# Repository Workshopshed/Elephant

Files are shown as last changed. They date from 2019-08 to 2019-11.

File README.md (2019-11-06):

# Elephant

This ESP32 controlled elephant was created for Diyode Magazine and was published in issue #26 and #28.  Daniel Koch took up the challenge to try to build this from my instructions and in the process we came up with a bunch of enhancements to make it easier to print and assemble. Daniel and Murray Roberts also ensured the wording of the instructions was top notch.

https://diyodemag.com/projects/part_1_walking_wildlife

https://diyodemag.com/projects/part_2_walking_wildlife

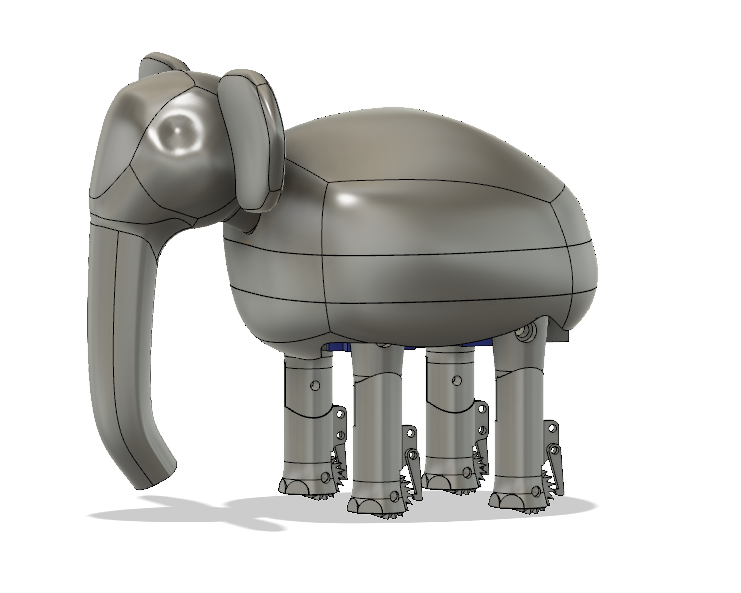
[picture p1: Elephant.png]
Elephant Model


The elephant is controlled from a simple web page hosted on the ESP32 and Ajax calls are used to respond to the buttons.

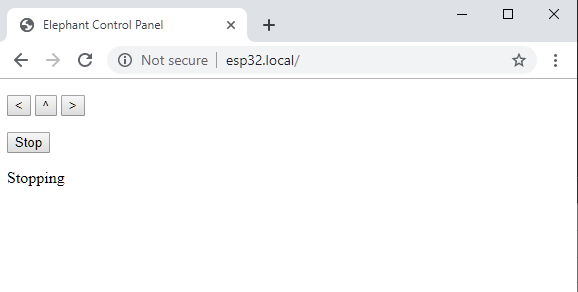
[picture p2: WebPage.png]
Web Page


A spin off project for the servo power distribution board also appeared in issue #26 with Daniel Koch providing a cloned version using stripboard.
https://diyodemag.com/projects/servo_power

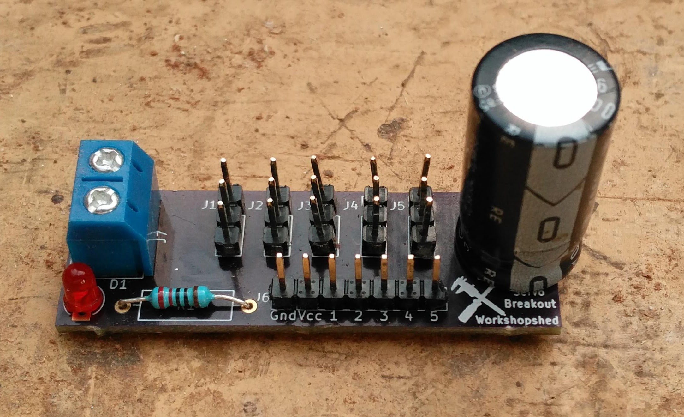
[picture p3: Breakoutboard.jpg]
Breakout Board


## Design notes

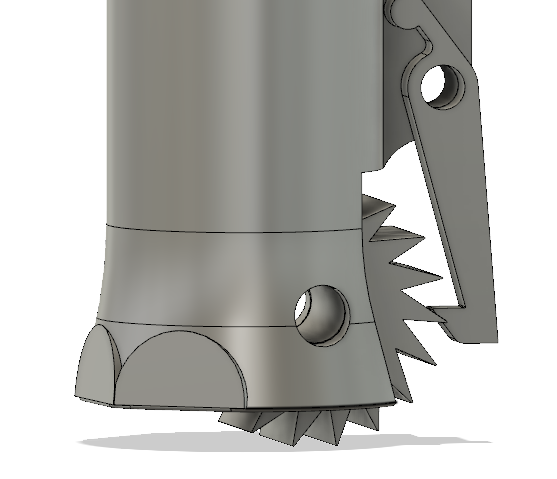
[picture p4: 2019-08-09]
RatchettMechanism.png

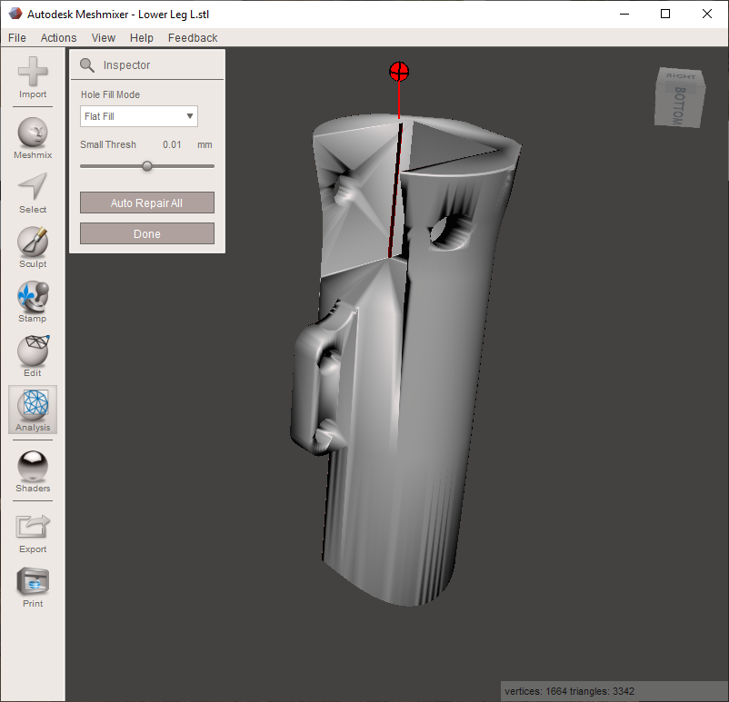
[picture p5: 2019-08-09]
MeshMixer.png

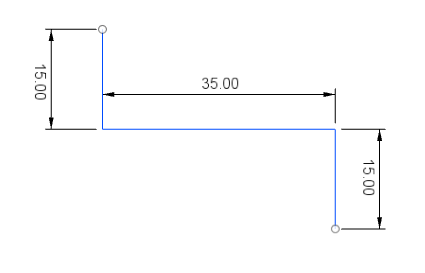
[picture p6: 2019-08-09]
WireTemplate.png

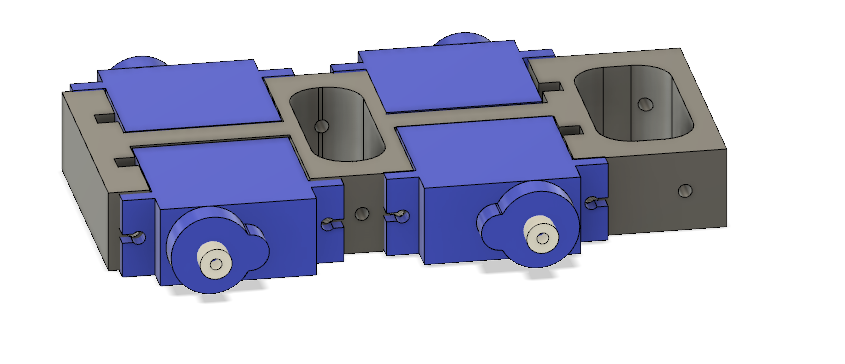
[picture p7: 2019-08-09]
Servos.png

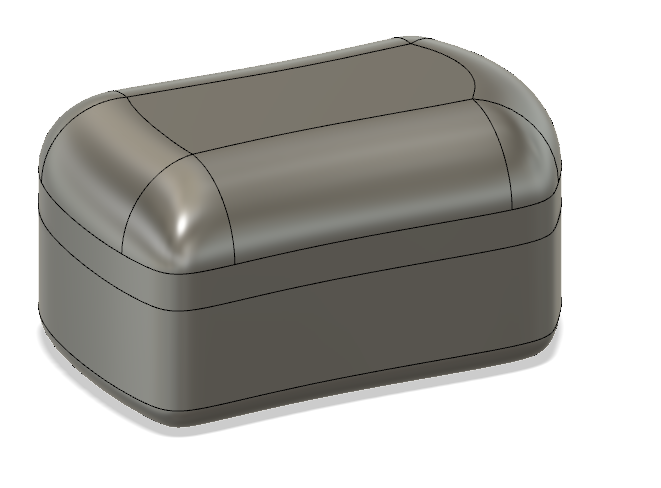
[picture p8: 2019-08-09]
SparePics/Boxy.png

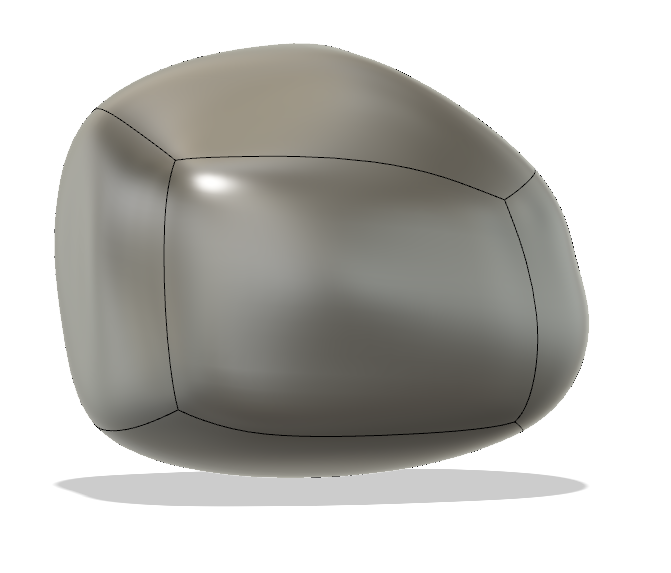
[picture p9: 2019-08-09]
SparePics/Form.png

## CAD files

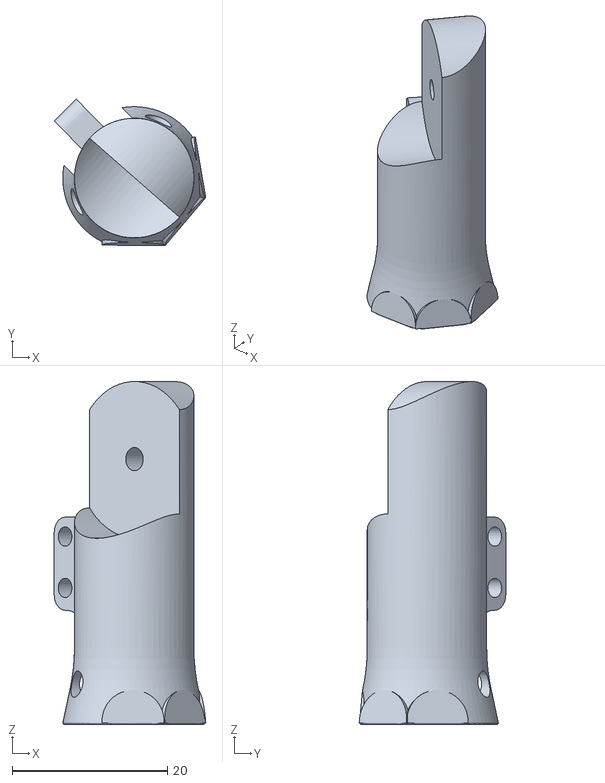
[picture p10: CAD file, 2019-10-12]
Models/Lower Leg L.stl
19.5 x 18.9 x 44.2

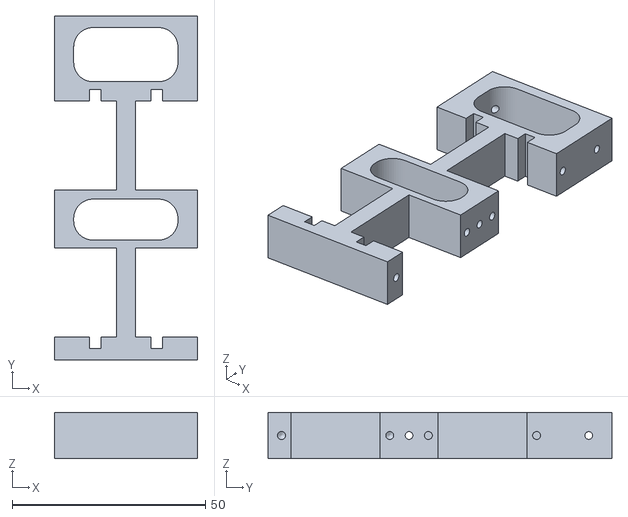
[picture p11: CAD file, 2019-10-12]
Models/Chassis.stl
37.0 x 89.0 x 12.0

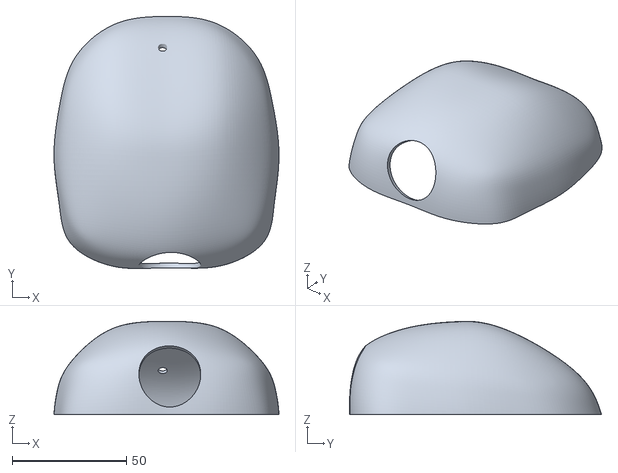
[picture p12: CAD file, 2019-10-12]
Models/Upper Body.stl
98.3 x 110.1 x 40.8

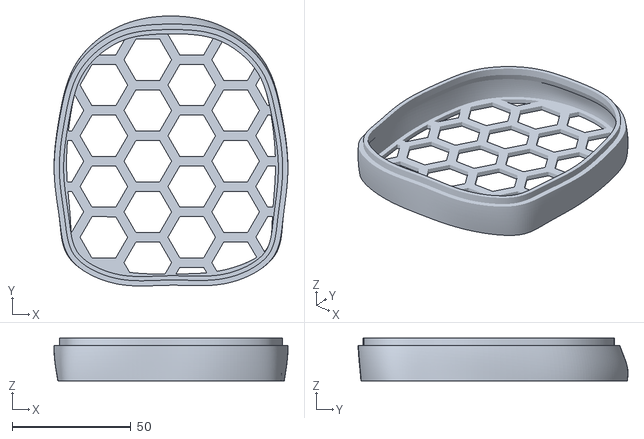
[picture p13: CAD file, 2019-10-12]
Models/Middle Body.stl
98.3 x 113.5 x 17.9

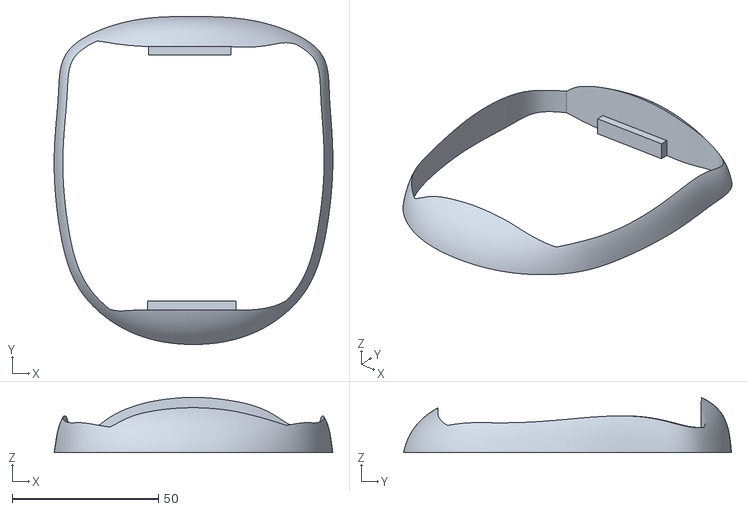
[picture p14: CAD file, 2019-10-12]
Models/Lower Body.stl
95.2 x 112.0 x 18.8

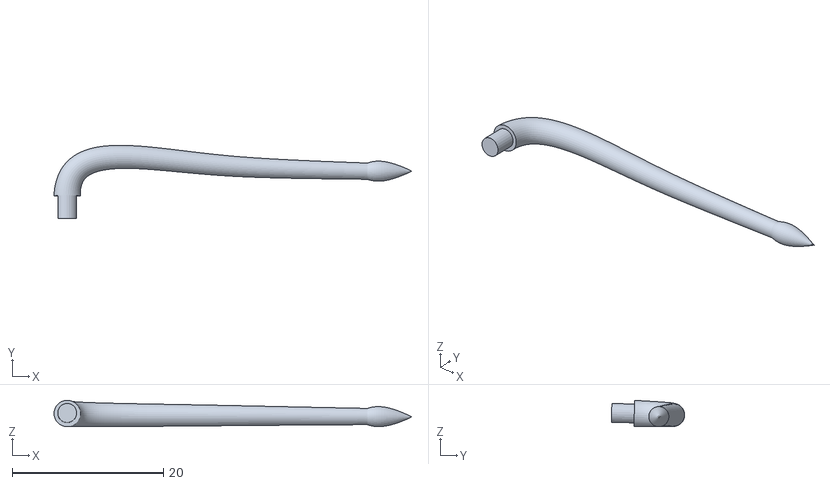
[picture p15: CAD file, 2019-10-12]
Models/Tail.stl
47.4 x 9.71 x 3.49

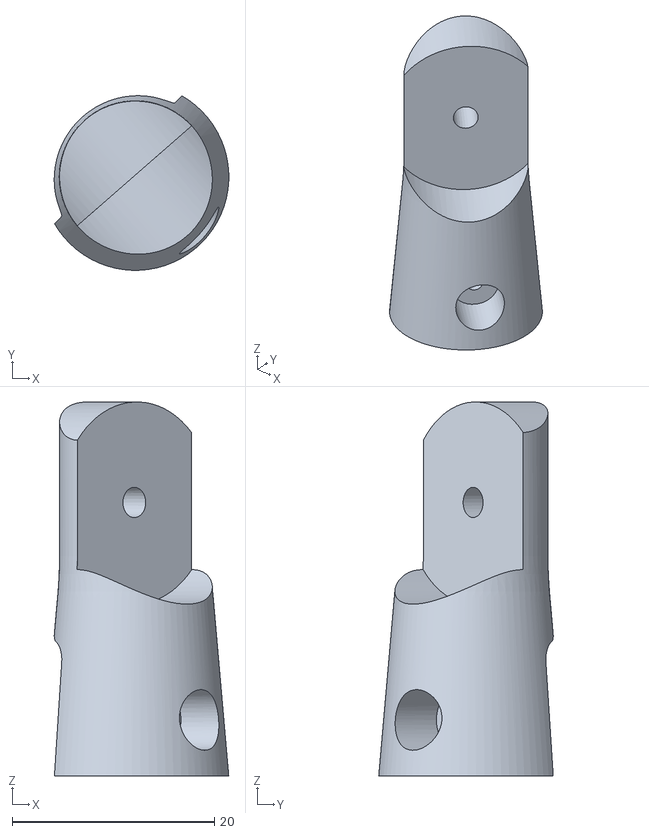
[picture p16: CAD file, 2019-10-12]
Models/Upper Leg.stl
17.3 x 17.3 x 37.0

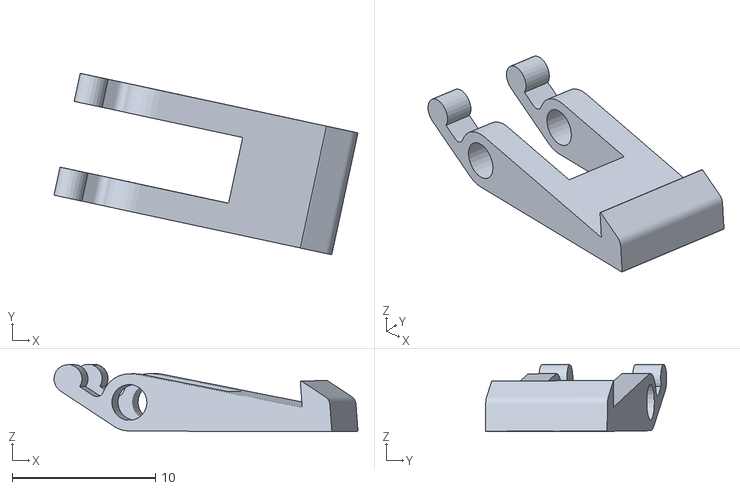
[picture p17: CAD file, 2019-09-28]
Models/Pawl.stl
21.2 x 12.7 x 4.71

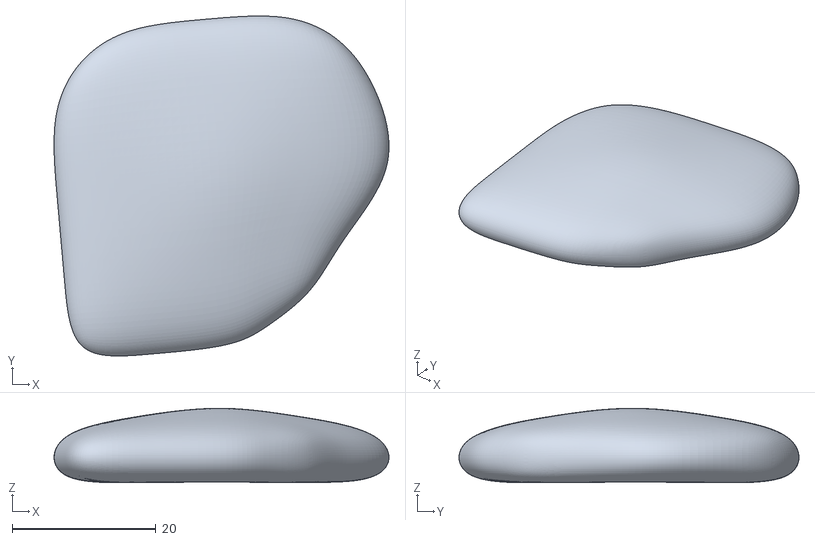
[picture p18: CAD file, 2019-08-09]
Models/EarR.stl
46.7 x 47.4 x 10.4

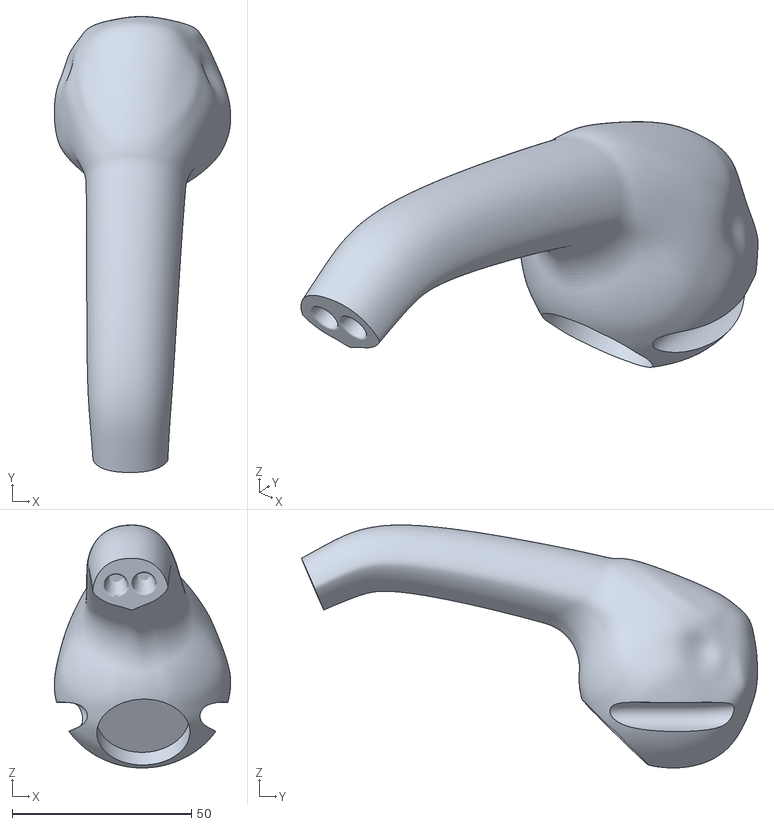
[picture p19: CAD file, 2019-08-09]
Models/Head.stl
49.2 x 127.2 x 67.8

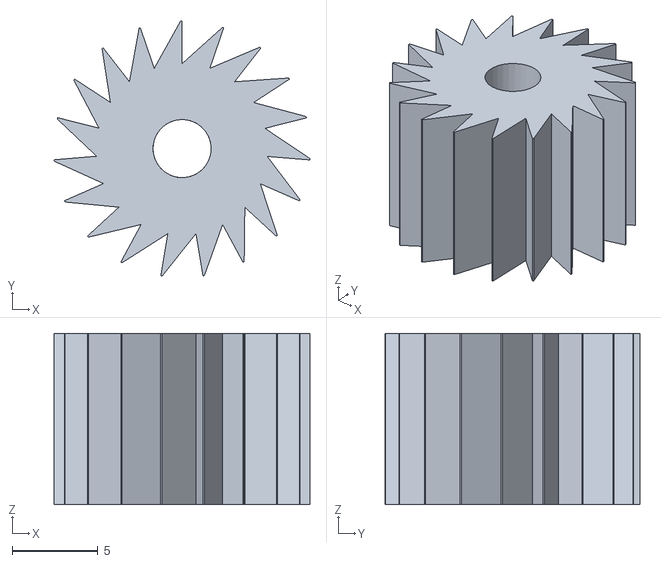
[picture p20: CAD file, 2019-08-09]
Models/Wheel.stl
15.0 x 14.9 x 10.0

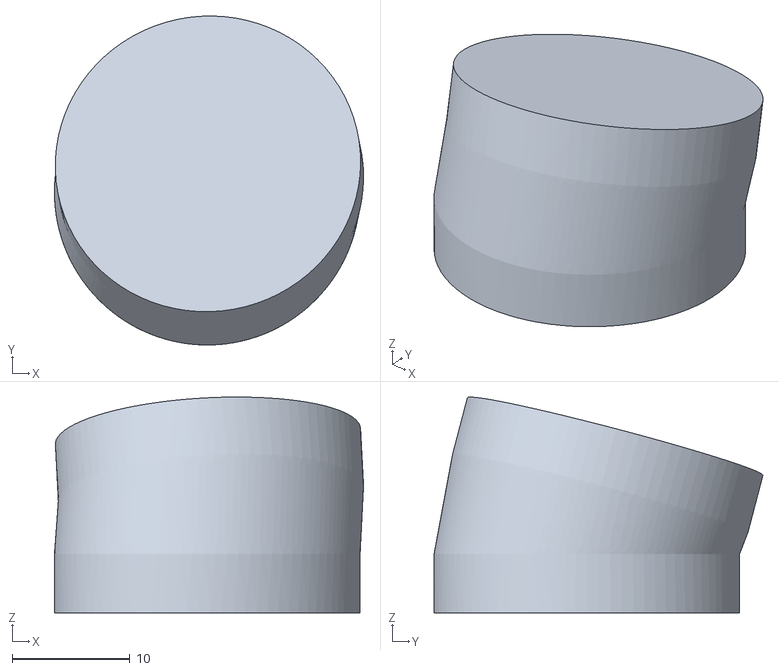
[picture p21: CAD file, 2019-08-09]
Models/Neck.stl
26.3 x 28.0 x 18.4

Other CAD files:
Models/Lower Leg R.stl
Models/EarL.stl

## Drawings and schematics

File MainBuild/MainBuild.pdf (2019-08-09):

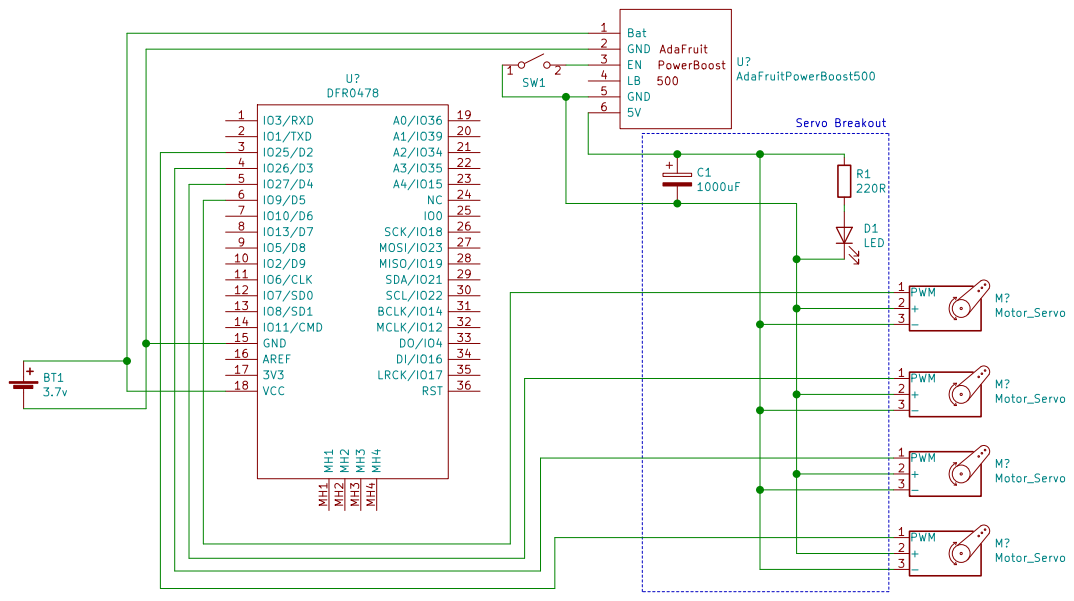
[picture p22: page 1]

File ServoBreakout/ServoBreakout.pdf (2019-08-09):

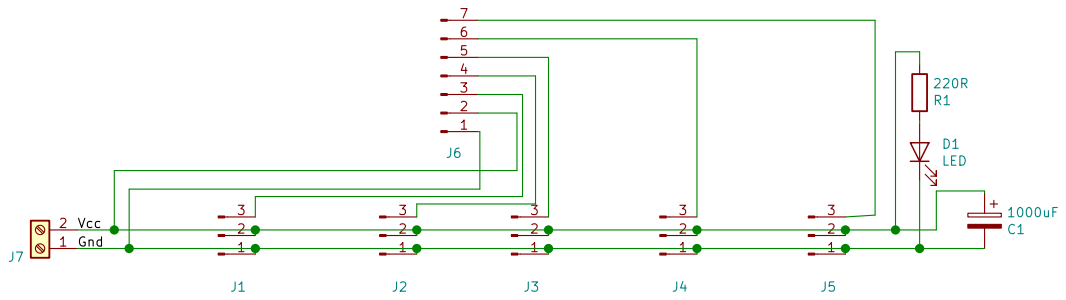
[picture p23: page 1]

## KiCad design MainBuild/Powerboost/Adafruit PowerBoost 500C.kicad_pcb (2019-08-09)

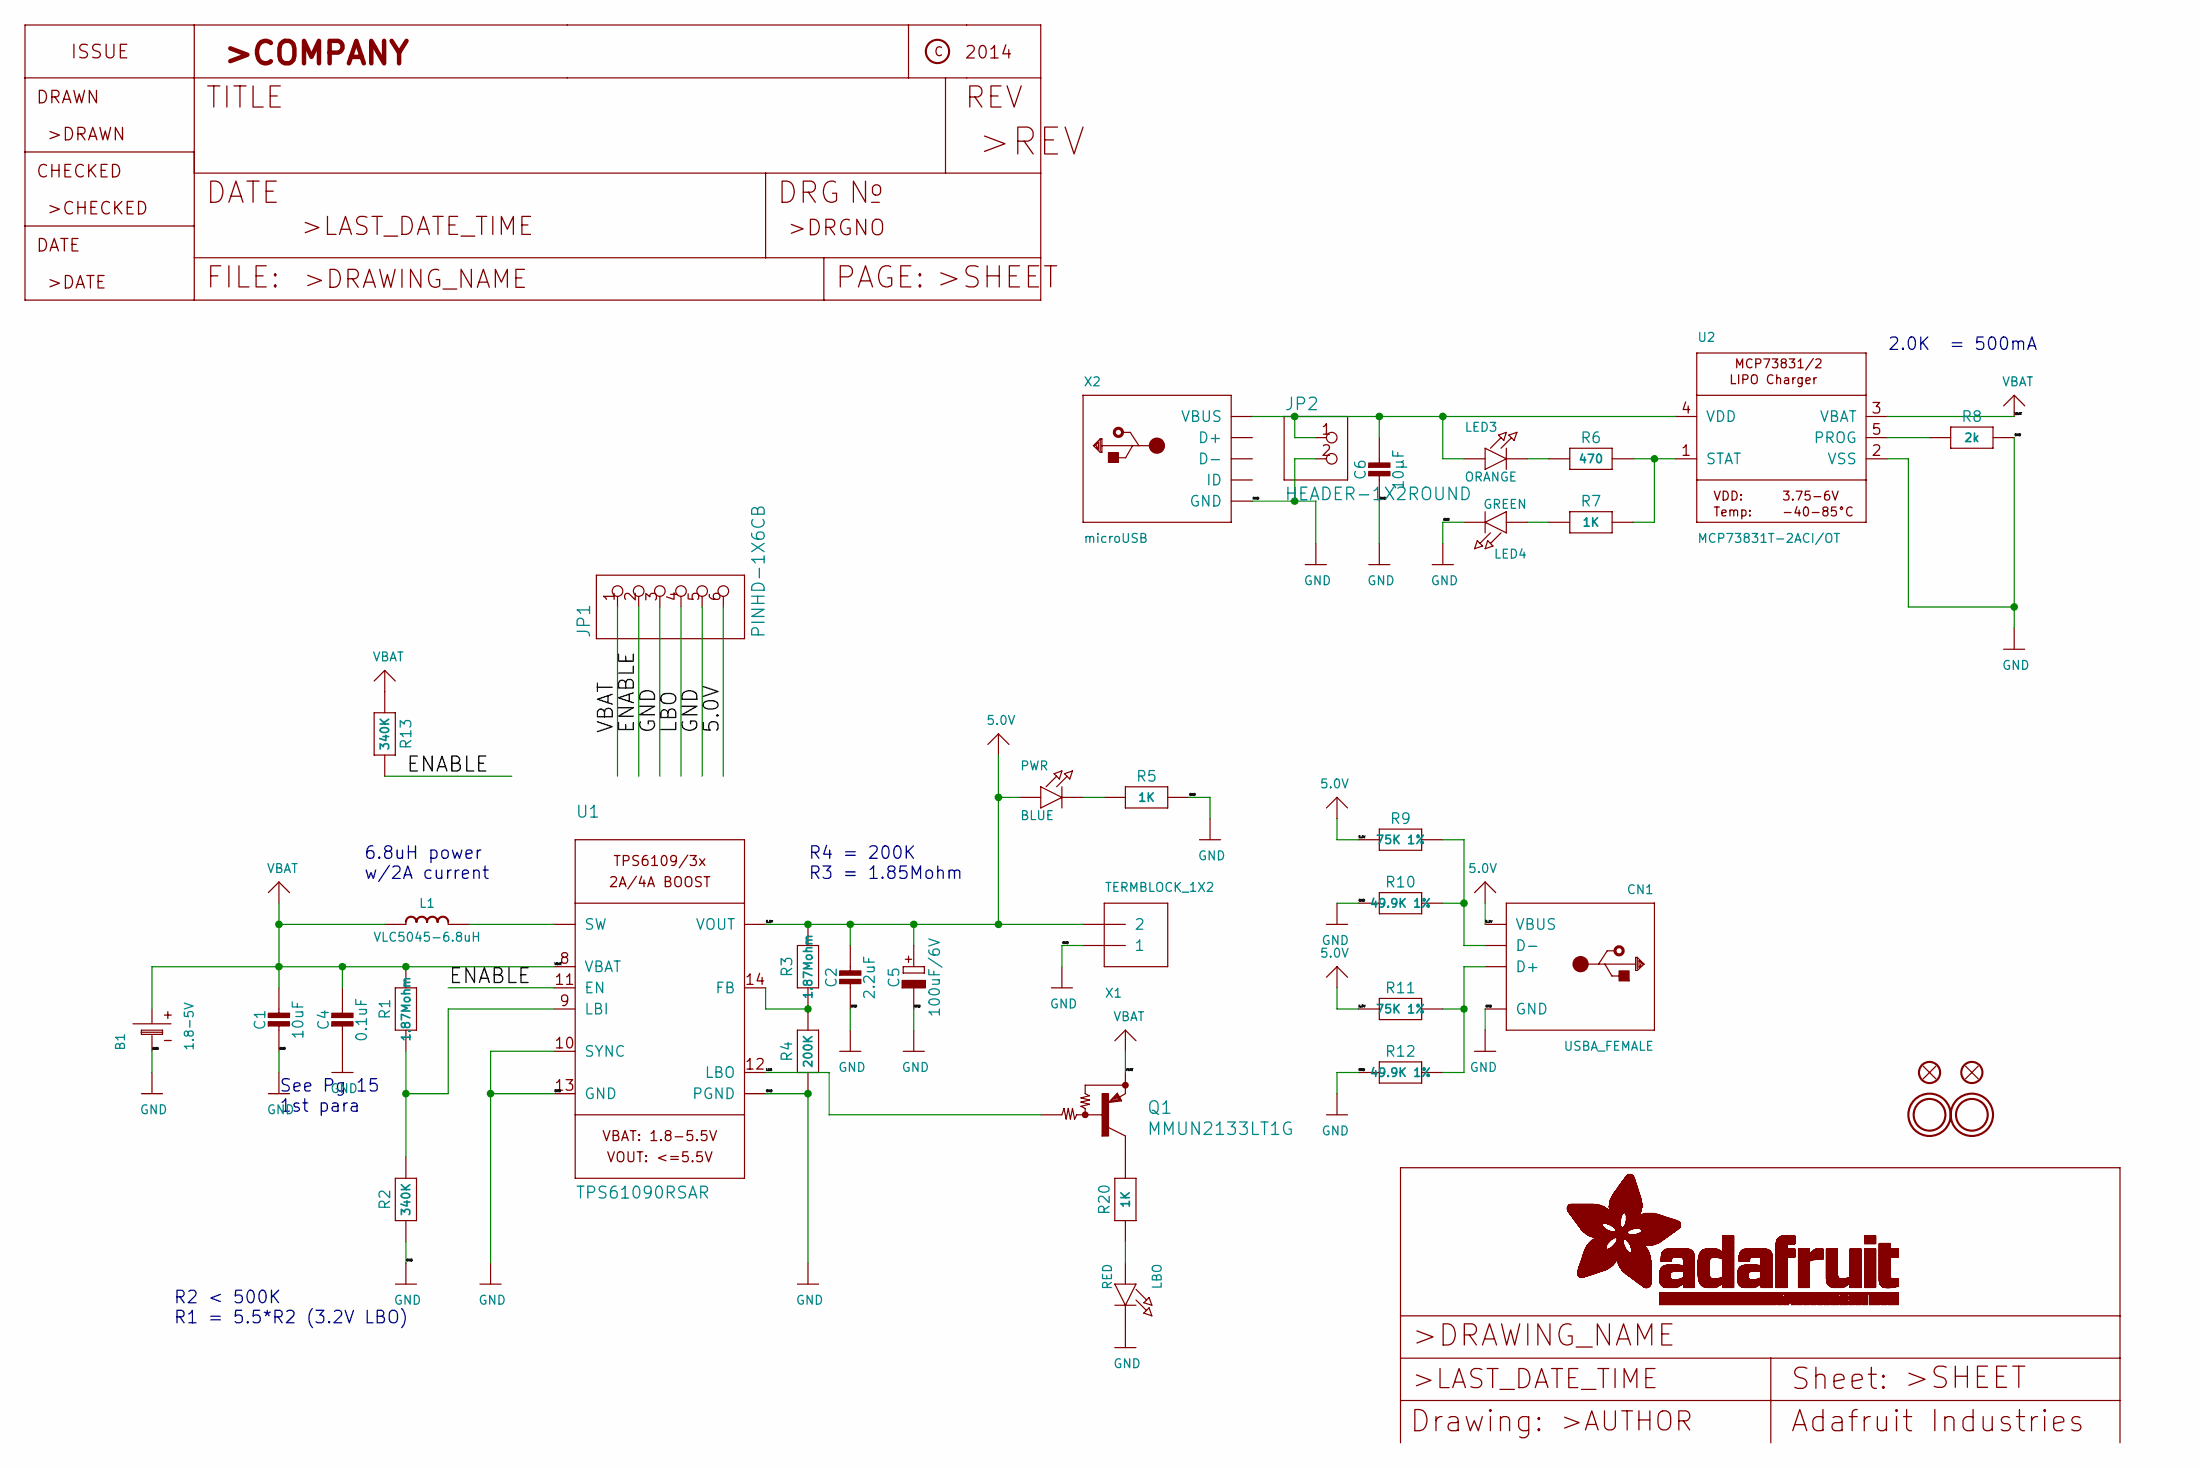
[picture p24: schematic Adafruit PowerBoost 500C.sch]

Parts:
B1: 1.8-5V; JSTPH2
C1: 10uF; 0805-NO
C2: 2.2uF; 0805-NO
C4: 0.1uF; 0805-NO
C5: 100uF/6V; EIA3528-21_B-R
C6: 10µF; 0805-NO
CN1: USBA_FEMALE; USB_HOST-PTH
FID2, FID3: FIDUCIAL\"\"; FIDUCIAL_1MM
JP1: PINHD-1X6CB; 1X06-CLEANBIG
JP2: HEADER-1X2ROUND; 1X02_ROUND
L1: VLC5045-6.8uH; INDUCTOR_5X5MM_TDK_VLC5045
LBO: RED; CHIPLED_0805_NOOUTLINE
LED3: ORANGE; CHIPLED_0805_NOOUTLINE
LED4: GREEN; CHIPLED_0805_NOOUTLINE
PWR: BLUE; CHIPLED_0805_NOOUTLINE
Q1: MMUN2133LT1G; SC59-BEC
R1, R3: 1.87Mohm; 0805-NO
R2, R13: 340K; 0805-NO
R4: 200K; 0805-NO
R5, R7, R20: 1K; 0805-NO
R6: 470; 0805-NO
R8: 2k; 0805-NO
R9, R11: 75K 1%; 0805-NO
R10, R12: 49.9K 1%; 0805-NO
U1: TPS61090RSAR; PVQFN-16
U2: MCP73831T-2ACI/OT; SOT23-5
U$10, U$12: MOUNTINGHOLE2.5; MOUNTINGHOLE_2.5_PLATED
X1: TERMBLOCK_1X2; TERMBLOCK_1X2-3.5MM
X2: microUSB; 4UCONN_20329

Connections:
5.0V: C2.1, C5.+, CN1.VBUS, JP1.6, PWR.A, R3.2, R9.2, R11.2, U1.1 (VOUT), U1.15 (VOUT), U1.16 (VOUT), X1.2; also elsewhere on the board
/ENABLE: JP1.2, R13.2, U1.11 (EN)
/LBO: JP1.4, Q1.B, U1.12 (LBO)
GND: B1.1 (-), C1.2, C2.2, C4.2, C5.-, C6.2, CN1.GND, JP1.3, JP1.5, JP2.2, LBO.C, LED4.C, R2.1, R4.1, R5.2, R8.2, R10.2, R12.2, U1.5 (PGND), U1.6 (PGND), U1.7 (PGND), U1.10 (SYNC), U1.13 (GND), U1.P$18 (PGND), U1.P$19 (PGND), U1.P$20 (PGND), U1.P$21 (PGND), U1.P$22 (PGND), U1.THERMAL (PGND), U2.2 (VSS), X1.1, X2.BASE@1 (GND), X2.BASE@2 (GND), X2.GND, X2.SPRT@1 (GND), X2.SPRT@2 (GND), X2.SPRT@3 (GND), X2.SPRT@4 (GND); also elsewhere on the board
unnamed: C6.1, JP2.1, LED3.A, U2.4 (VDD), X2.VBUS
unnamed: CN1.D+, R11.1, R12.1
unnamed: CN1.D-, R9.1, R10.1
unnamed: L1.P$2 (2), U1.3 (SW), U1.4 (SW)
unnamed 8: LBO.A, R20.1; also elsewhere on the board
unnamed: LED3.C, R6.1
unnamed: LED4.A, R7.1
unnamed 11: PWR.C, R5.1; also elsewhere on the board
unnamed: Q1.C, R20.2
unnamed: R1.1, R2.2, U1.9 (LBI)
unnamed: R3.1, R4.2, U1.14 (FB)
unnamed: R6.2, R7.2, U2.1 (STAT)
unnamed: R8.1, U2.5 (PROG)
VBAT: B1.2 (+), C1.1, C4.1, JP1.1, L1.P$1 (1), Q1.E, R1.2, R13.1, U1.8 (VBAT), U2.3 (VBAT)

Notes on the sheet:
See Pg 15 1st para
6.8uH power w/2A current
R2 < 500K R1 = 5.5*R2 (3.2V LBO)
R4 = 200K R3 = 1.85Mohm
2.0K = 500mA

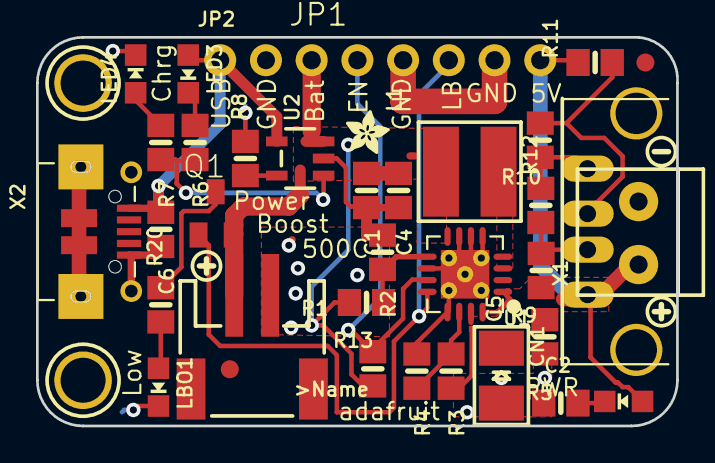
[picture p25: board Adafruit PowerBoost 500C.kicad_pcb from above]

Board: 2 copper layers, 35.6 x 21.6 mm, 42 parts (0 on the bottom side), 18 nets.

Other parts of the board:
LBO1: RED; CHIPLED_0805_NOOUTLINE
PWR1: BLUE; CHIPLED_0805_NOOUTLINE
U$13, U$25: SYMBOL_PLUS
U$26: SYMBOL_MINUS
U$28: ADAFRUIT_2.5MM
U$29: ADAFRUIT_5MM

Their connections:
5.0V: PWR1.A; also elsewhere on the board
GND: LBO1.C; also elsewhere on the board
unnamed 8: LBO1.A; also elsewhere on the board
unnamed 11: PWR1.C; also elsewhere on the board

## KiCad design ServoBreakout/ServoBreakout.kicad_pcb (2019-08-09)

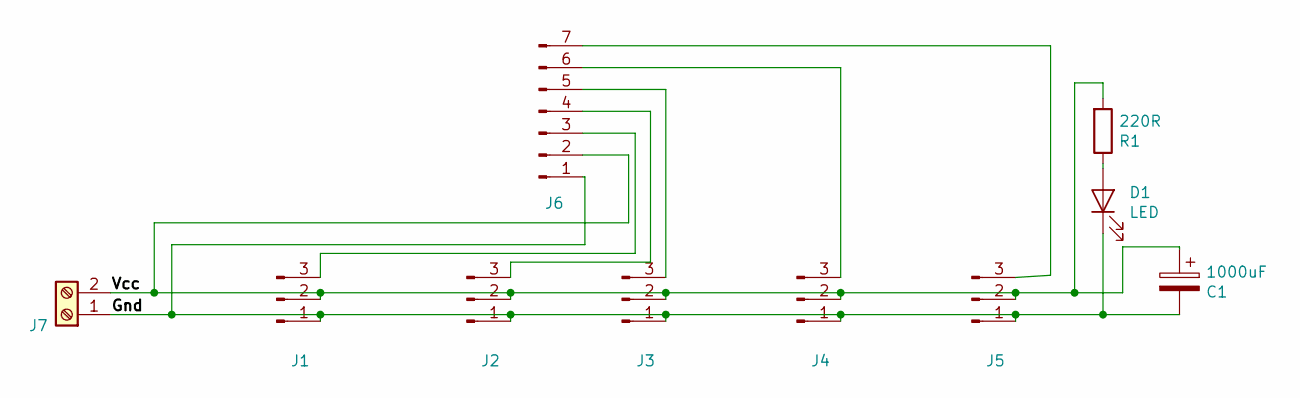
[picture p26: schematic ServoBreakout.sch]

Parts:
C1: 1000uF; CP_Radial_D10.0mm_P3.80mm
D1: LED; LED_D3.0mm
J1, J2, J3, J4, J5: Conn_01x03_Male; PinHeader_1x03_P2.54mm_Vertical
J6: Conn_01x07_Male; PinHeader_1x07_P2.54mm_Vertical
J7: Screw_Terminal_01x02; TerminalBlock_bornier-2_P5.08mm
R1: 220R; R_Axial_DIN0309_L9.0mm_D3.2mm_P12.70mm_Horizontal

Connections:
/Gnd: C1.2, D1.1 (K), J1.1, J2.1, J3.1, J4.1, J5.1, J6.1, J7.1
/Vcc: C1.1, J1.2, J2.2, J3.2, J4.2, J5.2, J6.2, J7.2, R1.2
unnamed: D1.2 (A), R1.1
unnamed: J1.3, J6.3
unnamed: J2.3, J6.4
unnamed: J3.3, J6.5
unnamed: J4.3, J6.6
unnamed: J5.3, J6.7

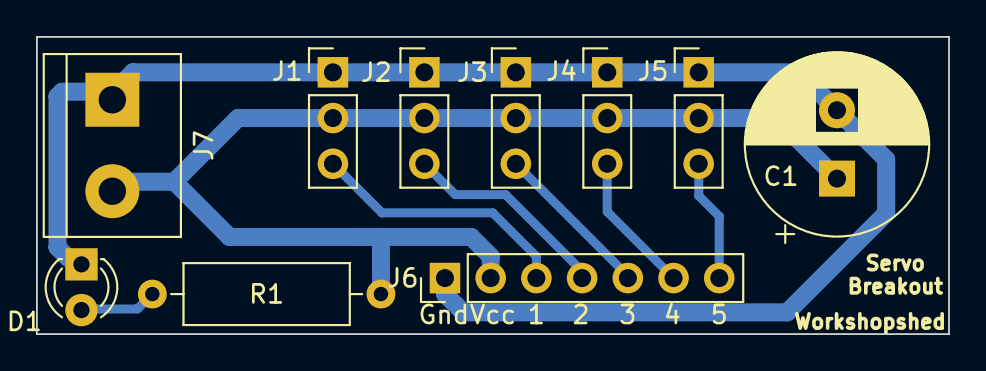
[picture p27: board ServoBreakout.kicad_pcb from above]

Board: 2 copper layers, 50.7 x 16.5 mm, 10 parts (0 on the bottom side), 8 nets.

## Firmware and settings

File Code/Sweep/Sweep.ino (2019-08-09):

/* Sweep
 *  Based on the work of BARRAGAN and Scott Fitzgerald  
 *  http://www.arduino.cc/en/Tutorial/Sweep
*/

#include <Servo.h>

Servo myservo[4];  

int position[4];   

int minpos = 50;
int maxpos = 120;
int slow = 1;
int fast = 4;

void setup() {
  // 3, 5, 6, 9
  myservo[0].attach(3);  
  myservo[1].attach(5);  
  myservo[2].attach(6);  
  myservo[3].attach(9);  
  
  position[0] = minpos;
  position[1] = maxpos;
  position[2] = minpos;
  position[3] = maxpos;
}

void moveServo(int servo, int speed) {
  myservo[servo].write(position[servo]);
  position[servo] = position[servo] + speed;
  if (position[servo] < minpos) { position[servo] = minpos; }
  if (position[servo] > maxpos) { position[servo] = maxpos; }
}

void loop() {
  for (int pos = minpos; pos <= maxpos; pos += 1) { 
        moveServo(0,slow);
        moveServo(1,-fast);
        moveServo(2,-slow);
        moveServo(3,fast);
        delay(15);
    }

  for (int pos = minpos; pos <= maxpos; pos += 1) { 
        moveServo(0,-fast);
        moveServo(1,slow);
        moveServo(2,fast);
        moveServo(3,-slow);
        delay(15);
    }
  
}

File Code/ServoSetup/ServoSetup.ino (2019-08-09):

/* Servo Setup, Move all to 90degrees - For Arduino Uno */

#include <Servo.h>

Servo myservo[4];  

void setup() {
  // 3, 5, 6, 9
  myservo[0].attach(3);  
  myservo[1].attach(5);  
  myservo[2].attach(6);  
  myservo[3].attach(9);  `
  
  position[0] = 90;
  position[1] = 90;
  position[2] = 90;
  position[3] = 90;
}

void loop() {
  sleep(1)
}

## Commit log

2019-08-09 Code, Models and Schematics
    [Adafruit PowerBoost 500C.kicad_pcb, Adafruit PowerBoost 500C.sch, Chassis.stl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]
2019-09-08 Update Lower Body.stl
    [Lower Body.stl]
2019-09-08 Revert "Update Lower Body.stl"
    This reverts commit 1fc1be777c2246e224255c42bd3ced255f698e47.
    [Lower Body.stl]
2019-09-28 Updated Models
    doubled up the pawl to stop it from flopping around on the bracket
    Added a hole for a servo horn into the leg
    [Pawl.stl, Upper Leg.stl]
2019-10-12 Update Upper Leg.stl
    New holes
    [Upper Leg.stl]
2019-10-12 Models
    Settled models on the bed
    [Chassis.stl, Lower Body.stl, Lower Leg L.stl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]
